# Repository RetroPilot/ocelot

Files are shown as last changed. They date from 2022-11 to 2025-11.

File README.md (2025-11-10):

# Welcome to Ocelot
something, something marketing. do we need to do this? if you don't know, prepare to know.

this is the firmware repository for RetroPilot's family of automotive gateway and control modules.

they allow users to easily retrofit parts from other cars, selectively gateway ECUs at will, filter and convert messages, control actuators, and more.

## Ocleot and Chimera

**[Gateway V2](https://shop.retropilot.org/product/gateway-v2/)** - the CAN gateway of your dreams. gateway messages between buses, retrofit parts, etc.
- gateway and modify CAN messages between multiple buses
- translate signals and convert message formats for part retrofitting
- filter and manipulate specific bits in CAN frames
- enable features by modifying ECU communications
- integrated SSR for connecting and disconnecting busses on-the-fly

**[Chimera](https://shop.retropilot.org/product/chimera/)** - CAN gateway with raw sensor inputs for complete vehicle integration
- has raw sensor inputs for VSS (vehicle speed), CPS (crank position sensor), and ADC (for cruise control stalks)
- can convert existing CAN messages to RetroPilot format for cars that already have some info available over CAN
- has OBD-C connector on-board for connecting to Comma devices
- has USB port on-board and panda-compatible API for sending/recieving messages over CAN
- ideal for vehicles that need CAN gatewaying and/or direct sensor processing in one device

## RetroPilot Cores

**[Actuator Core](https://shop.retropilot.org/product/actuator-core/)** - motor control for steering, throttle, or brake actuators and other automotive applications
- control two DC motors up to 6A each
- build custom actuators for steering, gas, brakes and more

**[Relay Core](https://shop.retropilot.org/product/relay-core/)** - GPIO and relay control with CAN integration
- control lights, fans, pumps, or other 12V devices via CAN messages or GPIO switches
- build custom lighting controllers that respond to vehicle state
- add remote-controlled accessories to your vehicle

**[Interceptor Core](https://shop.retropilot.org/product/interceptor-core/)** - analog sensor interception and injection
- intercept gas pedal signals and modify them for drive-by-wire applications
- modify torque sensor signals for custom steering feel
- add safety limits or filtering to analog sensor inputs

**⚠️ WARNING: Interceptor Core for steering applications is for RESEARCH AND DEVELOPMENT ONLY. Do not use on public roads. Use at your own risk with extreme caution, controlled environments, and always have backup safety systems. RetroPilot assumes no liability for any damages, injuries, or accidents.**

## Hardware
hardware is based on STM32F413 (most modules) or STM32F205 (pedal), and is fully OSHW where applicable. board files, bom, and schematics are located in the `hardware` folder.

## Firmware
firmware borrows heavily from [panda](https://github.com/commaai/panda), and should be firmware-compatible with Panda firmware as a black panda. conversely, most firmware should also work on a panda, which is helpful for development.

### Available Projects:
- `chimera` - Chimera gateway firmware
- `actuator_core` - motor control
- `relay_core` - relay and GPIO control  
- `interceptor_core` - analog sensor interception
- `ibst` - iBooster control
- `smart_dsu` - smart DSU module
- `eps_gw` - EPS gateway
- `steer_actuator_demo` - steering actuator demo
- `panda` - panda compatibility mode
- `pedal` - pedal module (STM32F205)

### Prerequisites:

#### Docker Setup (recommended):
install Docker for your operating system. then build the container:
```
./build_container.sh
```

#### Python Setup (for configuration tool):
install pipenv:
```
pip install pipenv
```
then setup the environment:
```
pipenv install
```

### Flashing:

Docker (recommended):
enter the environment
```
pipenv shell
```
you will want to do this any time you compile firmware, flash, or use the configuration tool. flash the board with
```
./flash_docker.sh <project name>
```

where <project_name> is the board or project you want to flash, for example actuator_core for Actuator Core. providing no arguments will list all projects available to build and flash.

### Configuration tool:

#### Mac/Linux:
enter the pipenv environment:
```
pipenv shell
```
then run the configuration tool:
```
./stm_flash_config.py
```
select the device you'd like to configure and follow the wizard.

##### Configuration by Device:

#### Actuator Core Configuration:

**System Config** - set device operating mode:
- `debug_lvl`: debug output level
- `can_out_en`: enable CAN message transmission
- `iwdg_en`: enable watchdog timer (0 while configuring, 1 when finished)
- `mode`: operating mode (0=Default/USB control, 1=Steer, 2=Cruise)

**TPS Config** - throttle position sensor setup (cruise mode only):
- `adc1`: minimum throttle position (fully closed)
- `adc2`: maximum throttle position (fully open)
- `adc_tolerance`: position control deadzone
- `adc_num`: ADC channel number (0 or 1)

**Motor Config** - throttle motor setup:
- `bridge_channel`: which H-bridge to use (1 or 2)
- `type`: motor function (1=throttle motor)
- `polarity`: motor direction (1=normal, 2=inverted)

**Clutch Config** - clutch motor setup:
- `bridge_channel`: which H-bridge to use (1 or 2)
- `type`: motor function (2=clutch)
- `polarity`: motor direction (1=normal, 2=inverted)

#### Interceptor Core Configuration:

**System Config** - set device operating mode:
- `debug_lvl`: debug output level
- `can_out_en`: enable CAN message transmission
- `iwdg_en`: enable watchdog timer (0 while configuring, 1 when finished)
- `mode`: operating mode (0=Unconfigured, 1=Differential, 2=Gas Pedal)
- `override_threshold`: differential mode threshold (default 336)

**ADC Channel Validation** - sensor validation setup:

*Differential Mode (center point + tolerance):*
- `adc1`: center value (expected sensor position)
- `adc2`: unused (set to 0)
- `adc_tolerance`: deviation tolerance (±)

*Gas Pedal Mode (range limits):*
- `adc1`: maximum valid value (e.g., 4000 for 4.0V)
- `adc2`: minimum valid value (e.g., 200 for 0.2V)
- `adc_tolerance`: hysteresis/noise tolerance

#### Relay Core Configuration:

**System Config** - basic system setup:
- `debug_lvl`: debug output level
- `can_out_en`: enable CAN message transmission
- `iwdg_en`: enable watchdog timer (0 while configuring, 1 when finished)

**Relay Configs** - individual relay setup:
- `label`: predefined automotive function (TURN_L_FRONT, HEAD_L, BRAKE_L, etc.)
- `gpio_en`: enable GPIO control (0 or 1)
- `gpio_bitmask`: GPIO pin combination required
- `can_addr`: CAN message ID to monitor (0 disables)
- `can_cmp_val`: CAN signal value that triggers relay
- `sig_len`/`shift_amt`: CAN signal extraction parameters

#### Chimera Configuration:

**System Config** - basic system setup:
- `debug_lvl`: debug output level
- `can_out_en`: enable CAN message transmission
- `iwdg_en`: enable watchdog timer (0 while configuring, 1 when finished)

**CAN Signal Configs** - gateway message processing:
- `can_id`: which CAN message to process (hex like 0x123)
- `shift_amt`/`sig_len`: which bits contain your signal (shift right X bits, then mask Y bits)
- `scale_mult`/`scale_offs`: math to convert raw values (result = raw * mult + offset)
- `endian_type`: byte order (0=little endian, 1=big endian)
- `is_signed`: treat signal as signed integer or not
- `enabled`: enable this signal processing (0 or 1)

**HALL Sensor Configs** - vehicle speed and engine sensor processing:
- `vss_ppd`: pulses per distance (mile or km)
- `is_km`: use metric units (1=km, 0=miles)
- `rel_cnt`: reluctor tooth count for crank position sensor
- `skipped_teeth`: missing teeth count (e.g., 36-1 = 1 skipped tooth)

**ADC Button Configs** - cruise control button detection:
- `adc1`/`adc2`: threshold values for button states
- `adc_tolerance`: noise tolerance
- `adc_num`: ADC channel for cruise control buttons

#### Any OS:
use the web-based config tool available [here](https://coreconfig.retropilot.org/)

## Documentation
full documentation and examples are available at the [RetroPilot Wiki](https://wiki.retropilot.org/index/hardware/ocelot):

https://wiki.retropilot.org/index/hardware/ocelot

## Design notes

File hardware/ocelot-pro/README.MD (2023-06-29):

# Ocelot Pro Hardware
This directory contains information related to Ocelot Pro hardare. Here, you'll find information about the hardware itself.
## Header Pin Description
### **H1: CAN**
This header contains the three CAN interfaces on the Ocelot Pro, and is organized like so:

| **CAN1** | **CAN2** | **CAN3** |
|---|---|---|
| CAN1L | CAN2L | CAN3L |
| CAN1H | CAN2H | CAN3H |

### **H2: SWD**
This header contains the pins to connect a SWD Link cable. You can use this along with GDB to debug the running application live.

### **H3: POWER**
This header is connected to all power rails in the Ocelot Pro. Each pin is duplicated in case you want to connect multiple peripherals to a rail.

| **PIN** | **Description** |
|---|---|
| IGN_OUT | 12V 3A, switched by pin PA1  |
| 12V | 12V input VIN |
| 5V | 5V 60mA |
| 3.3V | 3.3V 60mA |
| GND | Ground |

### **H4 and H5: GPIO**
All GPIO are 3.3V and connected directly to the STM32F413. Use a level shifter if using 5V logic. Best practice would be to limit the current source/sink to 25mA on a GPIO. More info on this in the datasheet.
Each GPIO can be used as digital I/O or alternate functions depending on the peripheral and the pin. See below:

#### **H4**
| **PIN** | **Alt Functions** |
|---|---|
| **PB10:** | TIM2_CH3, I2C2_SCL, SPI2_SCK/I2S2_CK, I2S3_MCK, USART3_TX, I2CFMP1_SCL, DFSDM2_CKOUT, SDIO_D7, EVENTOUT|
| **PB1:**  | TIM1_CH3N, TIM3_CH4, TIM8_CH3N, SPI5_NSS/I2S5_WS, DFSDM1_DATIN0, QUADSPI_CLK, EVENTOUT |
| **PC5:**  | DFSDM2_DATIN2, I2CFMP1_SMBA, USART3_RX, QUADSPI_BK2_IO3, FSMC_NOE, EVENTOUT |
| **PA7:**  | TIM1_CH1N, TIM3_CH2, TIM8_CH1N, SPI1_MOSI/I2S1_SD, DFSDM2_DATIN1, TIM14_CH1, QUADSPI_BK2_IO1, EVENTOUT |
| **PA5:**  | TIM2_CH1/TIM2_ETR, TIM8_CH1N, SPI1_SCK/I2S1_CK, DFSDM1_CKIN1, FSMC_D7/FSMC_DA7, EVENTOUT |
| **PA3:**  | TIM2_CH4, TIM5_CH4, TIM9_CH2, I2S2_MCK, USART2_RX, SAI1_SD_B, FSMC_D5/FSMC_DA5, EVENTOUT |
| **PC3:**  | LPTIM1_ETR, DFSDM2_CKIN7, SPI2_MOSI/I2S2_SD, SAI1_FS_B, FSMC_A0, EVENTOUT |
| **PC0:**  | LPTIM1_IN1, DFSDM2_CKIN4, SAI1_MCLK_B, EVENTOUT |
| **PC14:** | EVENTOUT |
| **3V3:**  | 3.3V rail |
| **PB2:**  | LPTIM1_OUT, DFSDM1_CKIN0, QUADSPI_CLK, EVENTOUT |
| **PB0:**  | TIM1_CH2N, TIM3_CH3, TIM8_CH2N, SPI5_SCK/I2S5_CK, EVENTOUT |
| **PC4:**  | DFSDM2_CKIN2, I2S1_MCK, QUADSPI_BK2_IO2, FSMC_NE4, EVENTOUT |
| **PA6:**  | TIM1_BKIN, TIM3_CH1, TIM8_BKIN, SPI1_MISO, I2S2_MCK, DFSDM2_CKIN1, TIM13_CH1, QUADSPI_BK2_IO0, SDIO_CMD, EVENTOUT | 
| **PA4:**  | SPI1_NSS/I2S1_WS, SPI3_NSS/I2S3_WS, USART2_CK, DFSDM1_DATIN1, FSMC_D6/FSMC_DA6, EVENTOUT |
| **PA2:**  | TIM2_CH3, TIM5_CH3, TIM9_CH1, I2S2_CKIN, USART2_TX, FSMC_D4/FSMC_DA4, EVENTOUT |
| **PC2:**  | LPTIM1_IN2, DFSDM2_DATIN7, SPI2_MISO, I2S2ext_SD, SAI1_SCK_B, DFSDM1_CKOUT, FSMC_NWE, EVENTOUT |
| **PC15:** | EVENTOUT |
| **NC:** | N/C |
| **GND:**  | Ground |

#### **H5**    
| **PIN** | **Alt Functions** |
|---|---|
| **PB12:** | TIM1_BKIN, I2C2_SMBA, SPI2_NSS/I2S2_WS, SPI4_NSS/I2S4_WS, SPI3_SCK/I2S3_CK, USART3_CK, CAN2_RX, DFSDM1_DATIN1, UART5_RX, FSMC_D13/FSMC_DA13, EVENTOUT | 
| **PB14:** | TIM1_CH2N, TIM8_CH2N, I2CFMP1_SDA, SPI2_MISO, I2S2ext_SD, USART3_RTS, DFSDM1_DATIN2, TIM12_CH1, FSMC_D0/FSMC_DA0, SDIO_D6, EVENTOUT | 
| **PC6:**  | TIM3_CH1, TIM8_CH1, I2CFMP1_SCL, I2S2_MCK, DFSDM1_CKIN3, DFSDM2_DATIN6, USART6_TX, FSMC_D1/FSMC_DA1, SDIO_D6, EVENTOUT |
| **PC8:**  | TIM3_CH3, TIM8_CH3, DFSDM2_CKIN3, USART6_CK, QUADSPI_BK1_IO2, SDIO_D0, EVENTOUT |
| **PA9:**  | TIM1_CH2, DFSDM2_CKIN3, I2C3_SMBA, SPI2_SCK/I2S2_CK, USART1_TX, USB_FS_VBUS, SDIO_D2, EVENTOUT |
| **PC10:** | DFSDM2_CKIN5, SPI3_SCK/I2S3_CK, USART3_TX, QUADSPI_BK1_IO1, SDIO_D2, EVENTOUT |
| **PC12:** | SPI3_MOSI/I2S3_SD, USART3_CK, UART5_TX, FSMC_D3/FSMC_DA3, SDIO_CK, EVENTOUT |
| **PB3:**  | TDO-SWO, TIM2_CH2, I2CFMP1_SDA, SPI1_SCK/I2S1_CK, SPI3_SCK/I2S3_CK, USART1_RX, UART7_RX, I2C2_SDA, SAI1_SD_A, CAN3_RX, EVENTOUT |
| **PB7:**  | LPTIM1_IN2, TIM4_CH2, I2C1_SDA, DFSDM2_DATIN7, USART1_RX, FSMC_NL, EVENTOUT |
| **3V3** | 3.3V rail |
|**PB13:**  | TIM1_CH1N, I2CFMP1_SMBA, SPI2_SCK/I2S2_CK, SPI4_SCK/I2S4_CK, USART3_CTS, CAN2_TX, DFSDM1_CKIN1, UART5_TX, EVENTOUT |
|**PB15:**  | RTC_REFIN, TIM1_CH3N, TIM8_CH3N, I2CFMP1_SCL, SPI2_MOSI/I2S2_SD, DFSDM1_CKIN2, TIM12_CH2, SDIO_CK, EVENTOUT |
|**PC7:** | TIM3_CH2, TIM8_CH2, I2CFMP1_SDA, SPI2_SCK/I2S2_CK, I2S3_MCK, DFSDM2_CKIN6, USART6_RX, DFSDM1_DATIN3, SDIO_D7, EVENTOUT |
|**PC9:** | MCO_2, TIM3_CH4, TIM8_CH4, I2C3_SDA, I2S2_CKIN, DFSDM2_DATIN3, QUADSPI_BK1_IO0, SDIO_D1, EVENTOUT |
|**PA10:**  | TIM1_CH3, DFSDM2_DATIN3, SPI2_MOSI/I2S2_SD, SPI5_MOSI/I2S5_SD, USART1_RX, USB_FS_ID, EVENTOUT |
|**PC11:**  | DFSDM2_DATIN5, I2S3ext_SD, SPI3_MISO, USART3_RX, UART4_RX, QUADSPI_BK2_NCS, FSMC_D2/FSMC_DA2, SDIO_D3, EVENTOUT |
|**PD2:** | TIM3_ETR, DFSDM2_CKOUT, UART5_RX, FSMC_NWE, SDIO_CMD, EVENTOUT |
|**PB4:** | JTRST, TIM3_CH1, SPI1_MISO, SPI3_MISO, I2S3ext_SD, UART7_TX, I2C3_SDA, SAI1_SCK_A, CAN3_TX, SDIO_D0, EVENTOUT |
|**N/C** | N/C |
|**GND** | Ground |

More info on GPIOs can be found in the [datasheet](https://www.st.com/resource/en/datasheet/stm32f423ch.pdf)

## Buttons, Connectors, and Jumpers
Ocelot Pro contains the following buttons:
BOOT (SW1)
RESET (SW2)

The RESET button resets the chip, and if the BOOT button is held while resetting, the device goes into DFU mode.

The USB-C connector is specifically used for CAN traffic analysis / serial debugging / firmware updates. Do not connect a Comma OBD-C cable into this port or you will risk burning up everything on the 5V rail.

## Board Files and Schematic
This directory contains the schematics and Gerber files for Ocelot Pro. Use these to customize the board or build one. Pre-made boards can be purchased at [RetroPilot Shop](https://shop.retropilot.org/product/ocelot-pro-devkit/)

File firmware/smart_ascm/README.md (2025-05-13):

# SmartASCM

## Supported cars
- 2023 Cadillac XT4

## How it Works
the GM brake message gets block by Smart ASCM and replaced with the one sent by the comma

## Installation

install the device with bus 1 connected to the chassis bus at ASCM (with ASCM removed from bus like GM cam harness), bus 2 connected to powertrain expansion at ASCM, and bus 3 connected to chassis of ASCM.

refer to the hardware guide for more info:
https://wiki.retropilot.org/index/hardware/ocelot/hardware

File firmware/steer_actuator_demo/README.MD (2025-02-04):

### Parts

| QTY | PN | Description | 
|-----|---|---|
|1 |BTS7960 | motor driver |
|2 |FIT0493 | 350RPM motor |
|1 |6656K236 | Ultra-Thin Ball Bearing, Steel Ring, Shielded, 60mm Shaft Diameter and 78mm Housing ID  |
|1 |Ocelot Pro | Ocelot Pro CAN Devkit |
|1 |89245-0K020| TOYOTA angle sensor |
|1 | - | 1kOhm Resistor |
|1 | - | toggle switch |

STL Files are in [here](../../hardware/actuator-demo) and were designed by David Abraham (@Vasillo on Discord)

Gear ratio between the motors and final drive gear is 5:1, thus the final torque output is around 9.414384 Nm at peak `((1.176798 Nm /motor * 2 motors) * 0.80 * 5)`

The 1k resistor pulls PB14 up to 3.3v, and the switch pulls the same pin to GND.

### Wiring

|  PIN  |  Function  |
|---|---|
| PB12  | L_ENABLE |
| PB13  | R_ENABLE |
| PB14  | SWITCH IN  |
| PA2 | L_PWM |
| PA3 | R_PWM |

Constant 12V should be used to power the Hbridge VBatt inputs, and a switched 12V should be used to connect the Ocelot Pro's 12V input to power.

#### Angle Sensor
CANL and CANH should be on the same bus as the Ocelot Pro CAN1. Below is a wiring guide.

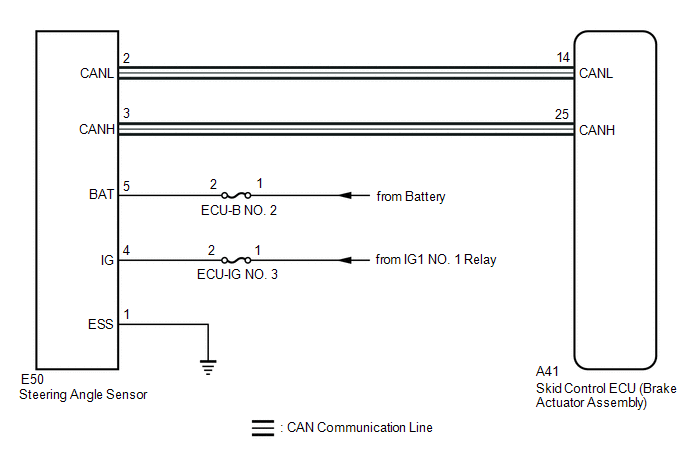
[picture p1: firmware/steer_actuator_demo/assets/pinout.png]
Angle Sensor Pinout


### CAN

This example only uses CAN1 to interface with CAN. Make sure to terminate the bus with a 120 Ohm resistor so everything communicates correctly.

#### Inputs:
0x22E - torque / angle request (angle req is not yet implemented)

#### Outputs:
0x22F - actuator status
0x22D - fake cruise state to engage OP demo

#### DBC Sample

```dbc
BO_ 741 STEERING_COMMAND: 5 EON
 SG_ REQUESTED_STEER_TORQUE : 29|11@1- (0.5,0) [-512|511.5] "Nm" EPAS
 SG_ COUNTER : 8|4@1+ (1,0) [0|15] "" EPAS
 SG_ REQUESTED_STEER_ANGLE : 14|15@1- (0.1,0) [-1638.4|1638.3] "deg" EPAS
 SG_ STEER_MODE : 12|2@1+ (1,0) [0|3] "" EPAS
 SG_ CHECKSUM : 0|8@1+ (1,0) [0|255] "" EPAS

BO_ 608 STEERING_STATUS: 5 EPAS
 SG_ COUNTER : 8|4@1+ (1,0) [0|15] "" EON
 SG_ STATUS : 12|4@1+ (1,0) [0|15] "" EON
 SG_ CHECKSUM : 0|8@1+ (1,0) [0|255] "" EON
 SG_ STEERING_TORQUE_EPS : 29|11@1- (0.8,0) [-819.2|818.4] "Nm" EON
 SG_ STEERING_TORQUE_DRIVER : 18|11@1- (0.8,0) [-819.2|818.4] "Nm" EON
 SG_ STEERING_OK : 16|1@1+ (1,0) [0|1] "" EON

BO_ 37 TOYOTA_STEERING_ANGLE_SENSOR1: 8 TOYOTASAS
 SG_ TOYOTA_STEER_RATE : 35|12@0- (1,0) [-2000|2000] "deg/s" EON
 SG_ TOYOTA_STEER_FRACTION : 39|4@0- (0.1,0) [-0.7|0.7] "deg" EON
 SG_ TOYOTA_STEER_ANGLE : 3|12@0- (1.5,0) [-500|500] "deg" EON

BO_ 870 CURRENT_STATE: 4 EON
 SG_ ENABLED : 8|1@1+ (1,0) [0|0] ""  HIM
 SG_ SET_SPEED : 16|8@1+ (1,0) [0|255] "mph"  HIM
 SG_ CURRENT_SPEED : 24|8@1+ (1,0) [0|255] "kph" IBST
 SG_ CHECKSUM : 0|8@1+ (1,0) [0|255] ""  HIM
```

### Openpilot
**Note: DO NOT UNDER ANY CIRCUMSTANCES INSTALL THIS ON A CAR. DO NOT ATTEMPT TO DRIVE WITH ANY OF THE HARDWARE OR SOFTWARE USED IN THIS DEMO. THIS DEMO IS RELEASED FOR RESEARCH PURPOSES ONLY, AND IS NOT MEANT TO BE USED ON PUBLIC ROADS. ALL INFORMATION AND SOFTWARE IS PROVIDED AS-IS.**

This demo uses an older version of OP that runs on the Eon/C2 or a PC. To connect it in, you will need a Panda (white/grey/black is fine) or a second Ocelot Pro with Panda Shield, relay, and dev harness.

Connect the 12Vbat line to 12V, and ignition to the same switched 12V ignition as the Ocelot. CAN1 and CAN3 from the Panda are bridged together and connected to the CAN bus containing the actuator and the Toyota SAS.

Install the following on an Eon or C2 device:

https://github.com/RetroPilot/openpilot

and checkout branch `actuator_demo`

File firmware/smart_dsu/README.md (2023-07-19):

# SmartDSU

## Supported cars
- 2017-2019 Toyota Corolla
- 2016-2018 Toyota Rav4 (and Hybrid)
- 2016-2019 Toyota Prius
- other DSU-equipped Toyotas with 0x343 as the ACC message

## Supported cars with slight firmware changes
- 2018 Camry Hybrid (tested by @halfcocked)
- 2022 RAV4 Hybrid (tested by @sky)

## How it Works
the Toyota ACC message 0x343 is read in on bus 3 of the gateway, modified, re-checksummed, then sent on to bus 1. if the ACC control message 0x343 is detected on bus 1, it will be blocked from bus 3 entirely. if the alt ACC control message 0xF10 is detected, the smartDSU will modify the forwarded 0x343 with data from inside 0xF10. this method ensures perfect message send rate preservation between the DSU and the vehicle CAN bus. 

a similar approach is taken with AEB message 0x344. if 0xF11 is detected on bus 1, the device will modify the Toyota AEB message, allowing for non-acc brake control without disturbing the stock AEB system.

all other messages are forwarded as-is between the DSU and the car.

if the device detects that 0xF10, 0xF11, or 0x343 is not sent, it will timeout functionality accordingly and restore forwarding between the DSU and the vehicle.

## Installation

install the device with bus 1 facing the CAR CAN and bus 3 facing the DSU or radar. ensure bus 3 is terminated by applying a blob of solder to JL2 (on ocelot pro) or the solder bridge next to CAN3 (on ocelot gateway.)

refer to the hardware guide for more info:
https://wiki.retropilot.org/index/hardware/ocelot/hardware

## Modifying for cars that do not require PERMIT_BRAKING and others
in main.c the following lines of code must be modified to prevent modification of the ACC message since it will be handled by Openpilot instead:

```c
          if(dat[7] == toyota_checksum(address, dat, 8)) {
            // add permit_braking and recompute the checksum
            dat[2] &= 0x3F; // mask off the top 2 bits
            dat[2] |= (1 << 6U); // SET_ME_X01
            dat[3] |= (1 << 6U); // permit_braking
            dat[7] = toyota_checksum(address, dat, 8); 
```

simply comment out the mask and the bitwise math:

```c
          if(dat[7] == toyota_checksum(address, dat, 8)) {
            // add permit_braking and recompute the checksum
            //dat[2] &= 0x3F; // mask off the top 2 bits
            //dat[2] |= (1 << 6U); // SET_ME_X01
            //dat[3] |= (1 << 6U); // permit_braking
            //dat[7] = toyota_checksum(address, dat, 8); 
```

and flash the firmware

```bash
cd ocelot/firmware/smart_dsu
# now put the device into recovery mode by holding BOOT and pressing RESET
./recover.sh
```

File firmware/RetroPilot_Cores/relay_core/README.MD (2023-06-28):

# Ocelot Pro GPIO example
## Introduction
This code functions as sort of an introduction to Ocelot / Panda / STM32 bare metal programming. The purpose is to show users how to set up interfaces on this platform using the Comma AI Panda codebase as a skeleton to build things on top. Maybe you want to build a CAN controlled relay and install it in a car. How would you go about doing that? Well a good place to start would be [Comma's Panda code](https://github.com/commaai/panda), since it aims to be compliant with MISRA and potentially ASIL. After that, it's a matter of grabbing an [Ocelot Pro](https://shop.retropilot.org/product/ocelot-pro-devkit/), setting up GPIOs, then connecting all that to the CAN interface so the GPIO responds to your custom CAN message.

That is where this example will hopefully help you out.

## What is covered here
We will do the following here:
- CAN interfaces setup (CAN1, CAN2, CAN3)
- Timer setup
- PWM setup
- GPIO setup

You will want a decent working knowledge of how to read code, preferably C. I'm not sure this would classify as a "beginner guide" per se, but if you're familiar with Arduino to some extent this should be somewhat approachable. We will not go too far in depth in terms of how the registers are actually set, nor what memory addresses and individual bits are actually set. So I guess difficulty: intermediate? Nothing to be scared of!

## Pins

PA2 - PWM (TIM5_CH3)
PA3 - PWM (TIM5_CH4)
PB12 - GPIO (digital out)
PB13 - GPIO (digital out)

Connect up to a scope, LEDs, h-bridge, whatever. Make sure to connect via a resistor (like 220 ohm or something) if using LEDs.

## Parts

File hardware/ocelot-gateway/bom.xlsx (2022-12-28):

No. | Quantity | Comment | Designator | Footprint | Value | Manufacturer Part | Manufacturer | Supplier Part | Supplier
1 | 2 | 22p | C1,C2 | 0603-C
2 | 2 | 4.7u | C3,C4 | 0603-C
3 | 10 | 100n | C5,C6,C7,C8,C9,C10,C11,C12,C13,C14 | 0603-C
4 | 2 | 2.2u | C15,C16 | 0603-C
5 | 1 | BAS40 | D1 | SOT23
6 | 1 | MIC5233-3.3YM5-TR | IC1 | SOT95P280X145-5N
7 | 1 |  | J1 | USB-C-BREAKOUT_SPARKFUN-CONNECTORS_USB-C-16P
8 | 3 |  | J2,J3,J4 | 1X02
9 | 1 |  | J5 | 1X04
10 | 1 |  | J6 | 1X05_1.27MM
11 | 1 | MIC5233-5.0YM5-TR | PS1 | SOT95P280X145-5N
12 | 1 | PMOSFET | Q1 | SOT23
13 | 1 | NMOSFET | Q2 | SOT23
14 | 2 | 22 | R1,R2 | 0402-R
15 | 2 | 5.1k | R3,R4 | 0402-R
16 | 2 | 120 | R5,R6 | 0402-R
17 | 4 | 10k | R7,R8,R9,R10 | 0402-R
18 | 2 | MOMENTARY-SWITCH-SPST-SMD-6.0X3.5MM | S1,S2 | TACTILE_SWITCH_SMD_6.0X3.5MM
19 | 2 |  | SJ1,SJ2 | SJ
20 | 1 | STM32F413RGT6 | U1 | LQFP64-10X10MM
21 | 3 | TJA1042 | U2,U3,U4 | NXP_SEMICONDUCTORS_TJA1042T-3-CM_118_0
22 | 1 | CRYSTAL-3.2X2.54-PIN | Y1 | XTAL-3.2X2.5

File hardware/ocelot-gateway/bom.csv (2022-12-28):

Part | Value | Device | Package | Description
C1 | 22p | C0603 | 0603-C
C2 | 22p | C0603 | 0603-C
C3 | 4.7u | C0603 | 0603-C
C4 | 4.7u | C0603 | 0603-C
C5 | 100n | C0603 | 0603-C
C6 | 100n | C0603 | 0603-C
C7 | 100n | C0603 | 0603-C
C8 | 100n | C0603 | 0603-C
C9 | 100n | C0603 | 0603-C
C10 | 100n | C0603 | 0603-C
C11 | 100n | C0603 | 0603-C
C12 | 100n | C0603 | 0603-C
C13 | 100n | C0603 | 0603-C
C14 | 100n | C0603 | 0603-C
C15 | 2.2u | C0603 | 0603-C
C16 | 2.2u | C0603 | 0603-C
D1 | BAS40 | BAS40 | SOT23 | Silicon Schottky Diodes
IC1 | MIC5233-3.3YM5-TR | MIC5233-3.3YM5-TR | SOT95P280X145-5N | High Input Voltage Low IQ UCAP LDO Regulator
J1 |  | USB-C-BREAKOUT_SPARKFUN-CONNECTORS_USB_C16PIN | USB-C-BREAKOUT_SPARKFUN-CONNECTORS_USB-C-16P | USB Type C 16Pin Connector
J2 |  | CONN_02 | 1X02 | Multi connection point. Often used as Generic Header-pin footprint for 0.1 inch
J3 |  | CONN_02 | 1X02 | Multi connection point. Often used as Generic Header-pin footprint for 0.1 inch
J4 |  | CONN_02 | 1X02 | Multi connection point. Often used as Generic Header-pin footprint for 0.1 inch
J5 |  | CONN_04 | 1X04 | Multi connection point. Often used as Generic Header-pin footprint for 0.1 inch
PS1 | MIC5233-5.0YM5-TR | MIC5233-5.0YM5-TR | SOT95P280X145-5N | MICROCHIP - MIC5233-5.0YM5-TR - LDO, REG, 36VIN, 0.1A, 5V, 2%, 5SOT23
Q1 | PMOSFET | PMOSFET_SOT23 | SOT23 | P-Channel MOSFET - Generic
Q2 | NMOSFET | NMOSFETSOT23 | SOT23 | N-Channel MOSFET - Generic
R1 | 22 | R0402 | 0402-R
R2 | 22 | R0402 | 0402-R
R3 | 5.1k | R0402 | 0402-R
R4 | 5.1k | R0402 | 0402-R
R5 | 120 | R0402 | 0402-R
R6 | 120 | R0402 | 0402-R
R7 | 10k | R0402 | 0402-R
R8 | 10k | R0402 | 0402-R
R9 | 10k | R0402 | 0402-R
R10 | 10k | R0402 | 0402-R
S1 | MOMENTARY-SWITCH-SPST-SMD-6.0X3.5MM | MOMENTARY-SWITCH-SPST-SMD-6.0X3.5MM | TACTILE_SWITCH_SMD_6.0X3.5MM | Momentary Switch (Pushbutton) - SPST
S2 | MOMENTARY-SWITCH-SPST-SMD-6.0X3.5MM | MOMENTARY-SWITCH-SPST-SMD-6.0X3.5MM | TACTILE_SWITCH_SMD_6.0X3.5MM | Momentary Switch (Pushbutton) - SPST
SJ1 |  | SJ | SJ | SMD solder JUMPER
SJ2 |  | SJ | SJ | SMD solder JUMPER
U1 | STM32F413RGT6 | STM32F413RGT6 | LQFP64-10X10MM
U2 | TJA1042 | TJA1042 | NXP_SEMICONDUCTORS_TJA1042T-3-CM_118_0
U3 | TJA1042 | TJA1042 | NXP_SEMICONDUCTORS_TJA1042T-3-CM_118_0
U4 | TJA1042 | TJA1042 | NXP_SEMICONDUCTORS_TJA1042T-3-CM_118_0
Y1 | CRYSTAL-3.2X2.54-PIN | CRYSTAL-3.2X2.54-PIN | XTAL-3.2X2.5

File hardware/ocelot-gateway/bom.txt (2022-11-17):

Part Value                               Device                                        Package                                      Description                                                                                                     BUILT_BY    CATEGORY   COPYRIGHT                                                   DESCRIPTION                                                           DRAIN_CURRENT HEIGHT MANUFACTURER MANUFACTURER_NAME MANUFACTURER_PART_NUMBER MOUSER_PART_NUMBER   MOUSER_PRICE-STOCK                                                                                                  MPN OPERATING_TEMP PART_STATUS POPULARITY PROD_ID    ROHS_COMPLIANT SERIES SF_SKU    SOURCELIBRARY                  SUB-CATEGORY THERMALLOSS TYPE      VALUE   VENDOR            
C1   22p                                 C0603                                         0603-C                                                                                                                                                                                                                                                                                                                                                                                                                                                                                                                                                                                                                                                                                                                       
C2   22p                                 C0603                                         0603-C                                                                                                                                                                                                                                                                                                                                                                                                                                                                                                                                                                                                                                                                                                                       
C3   4.7u                                C0603                                         0603-C                                                                                                                                                                                                                                                                                                                                                                                                                                                                                                                                                                                                                                                                                                                       
C4   4.7u                                C0603                                         0603-C                                                                                                                                                                                                                                                                                                                                                                                                                                                                                                                                                                                                                                                                                                                       
C5   100n                                C0603                                         0603-C                                                                                                                                                                                                                                                                                                                                                                                                                                                                                                                                                                                                                                                                                                                       
C6   100n                                C0603                                         0603-C                                                                                                                                                                                                                                                                                                                                                                                                                                                                                                                                                                                                                                                                                                                       
C7   100n                                C0603                                         0603-C                                                                                                                                                                                                                                                                                                                                                                                                                                                                                                                                                                                                                                                                                                                       
C8   100n                                C0603                                         0603-C                                                                                                                                                                                                                                                                                                                                                                                                                                                                                                                                                                                                                                                                                                                       
C9   100n                                C0603                                         0603-C                                                                                                                                                                                                                                                                                                                                                                                                                                                                                                                                                                                                                                                                                                                       
C10  100n                                C0603                                         0603-C                                                                                                                                                                                                                                                                                                                                                                                                                                                                                                                                                                                                                                                                                                                       
C11  100n                                C0603                                         0603-C                                                                                                                                                                                                                                                                                                                                                                                                                                                                                                                                                                                                                                                                                                                       
C12  100n                                C0603                                         0603-C                                                                                                                                                                                                                                                                                                                                                                                                                                                                                                                                                                                                                                                                                                                       
C13  100n                                C0603                                         0603-C                                                                                                                                                                                                                                                                                                                                                                                                                                                                                                                                                                                                                                                                                                                       
C14  100n                                C0603                                         0603-C                                                                                                                                                                                                                                                                                                                                                                                                                                                                                                                                                                                                                                                                                                                       
C15  2.2u                                C0603                                         0603-C                                                                                                                                                                                                                                                                                                                                                                                                                                                                                                                                                                                                                                                                                                                       
C16  2.2u                                C0603                                         0603-C                                                                                                                                                                                                                                                                                                                                                                                                                                                                                                                                                                                                                                                                                                                       
D1   BAS40                               BAS40                                         SOT23                                        Silicon Schottky Diodes                                                                                                                                                                                                                                                                                                                                                                                                                                                                                                       0                                                                                                                                                 
IC1  MIC5233-3.3YM5-TR                   MIC5233-3.3YM5-TR                             SOT95P280X145-5N                             High Input Voltage Low IQ UCAP LDO Regulator                                                                                                                                                       High Input Voltage Low IQ UCAP LDO Regulator                                        1.45mm              Microchip         MIC5233-3.3YM5-TR        998-MIC5233-3.3YM5TR https://www.mouser.co.uk/ProductDetail/Microchip-Technology-Micrel/MIC5233-33YM5-TR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                                                                                                                                                                                  
J1                                       USB-C-BREAKOUT_SPARKFUN-CONNECTORS_USB_C16PIN USB-C-BREAKOUT_SPARKFUN-CONNECTORS_USB-C-16P USB Type C 16Pin Connector                                                                                                                                                                                                                                                                                                                                                                                                                                                                                                               CONN-14122                                                                                                                             
J2                                       CONN_02                                       1X02                                         Multi connection point. Often used as Generic Header-pin footprint for 0.1 inch spaced/style header connections                                                                                                                                                                                                                                                                                                                                                                                                                                                                                                                                                                 
J3                                       CONN_02                                       1X02                                         Multi connection point. Often used as Generic Header-pin footprint for 0.1 inch spaced/style header connections                                                                                                                                                                                                                                                                                                                                                                                                                                                                                                                                                                 
J4                                       CONN_02                                       1X02                                         Multi connection point. Often used as Generic Header-pin footprint for 0.1 inch spaced/style header connections                                                                                                                                                                                                                                                                                                                                                                                                                                                                                                                                                                 
J5                                       CONN_04                                       1X04                                         Multi connection point. Often used as Generic Header-pin footprint for 0.1 inch spaced/style header connections                                                                                                                                                                                                                                                                                                                                                                                                                          CONN-09696                                                                                                                             
PS1  MIC5233-5.0YM5-TR                   MIC5233-5.0YM5-TR                             SOT95P280X145-5N                             MICROCHIP - MIC5233-5.0YM5-TR - LDO, REG, 36VIN, 0.1A, 5V, 2%, 5SOT23                                                                                                                              MICROCHIP - MIC5233-5.0YM5-TR - LDO, REG, 36VIN, 0.1A, 5V, 2%, 5SOT23               1.45mm              Microchip         MIC5233-5.0YM5-TR        998-MIC5233-5.0YM5TR https://www.mouser.co.uk/ProductDetail/Microchip-Technology-Micrel/MIC5233-50YM5-TR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                                                                                                                                                                                  
Q1   PMOSFET                             PMOSFET_SOT23                                 SOT23                                        P-Channel MOSFET - Generic                                                                                                  Transistor                                                                                                                                                                                                                                                                                                                                                                                                                                                                             MOSFET                   P-Channel PMOSFET                   
Q2   NMOSFET                             NMOSFETSOT23                                  SOT23                                        N-Channel MOSFET - Generic                                                                                                  Transistor                                                                                                                                                                                                                                                                                                                                                                                                                                                                             MOSFET                   N-Channel NMOSFET                   
R1   22                                  R0402                                         0402-R                                                                                                                                                                                                                                                                                                                                                                                                                                                                                                                                                                                                                                                                                                                       
R2   22                                  R0402                                         0402-R                                                                                                                                                                                                                                                                                                                                                                                                                                                                                                                                                                                                                                                                                                                       
R3   5.1k                                R0402                                         0402-R                                                                                                                                                                                                                                                                                                                                                                                                                                                                                                                                                                                                                                                                                                                       
R4   5.1k                                R0402                                         0402-R                                                                                                                                                                                                                                                                                                                                                                                                                                                                                                                                                                                                                                                                                                                       
R5   120                                 R0402                                         0402-R                                                                                                                                                                                                                                                                                                                                                                                                                                                                                                                                                                                                                                                                                                                       
R6   120                                 R0402                                         0402-R                                                                                                                                                                                                                                                                                                                                                                                                                                                                                                                                                                                                                                                                                                                       
R7   10k                                 R0402                                         0402-R                                                                                                                                                                                                                                                                                                                                                                                                                                                                                                                                                                                                                                                                                                                       
R8   10k                                 R0402                                         0402-R                                                                                                                                                                                                                                                                                                                                                                                                                                                                                                                                                                                                                                                                                                                       
R9   10k                                 R0402                                         0402-R                                                                                                                                                                                                                                                                                                                                                                                                                                                                                                                                                                                                                                                                                                                       
R10  10k                                 R0402                                         0402-R                                                                                                                                                                                                                                                                                                                                                                                                                                                                                                                                                                                                                                                                                                                       
S1   MOMENTARY-SWITCH-SPST-SMD-6.0X3.5MM MOMENTARY-SWITCH-SPST-SMD-6.0X3.5MM           TACTILE_SWITCH_SMD_6.0X3.5MM                 Momentary Switch (Pushbutton) - SPST                                                                                                                                                                                                                                                                                                                                                                                                                                                                                                     SWCH-00815                       COM-08229
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

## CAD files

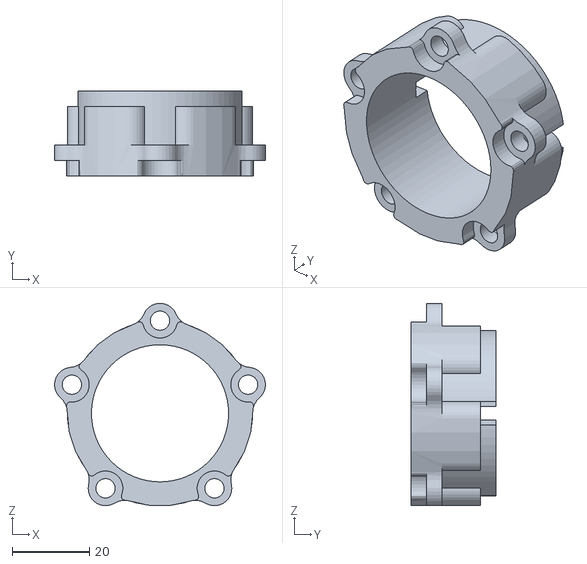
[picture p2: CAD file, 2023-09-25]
hardware/actuator-demo/sas_ring.stl
54.6 x 22.0 x 52.4

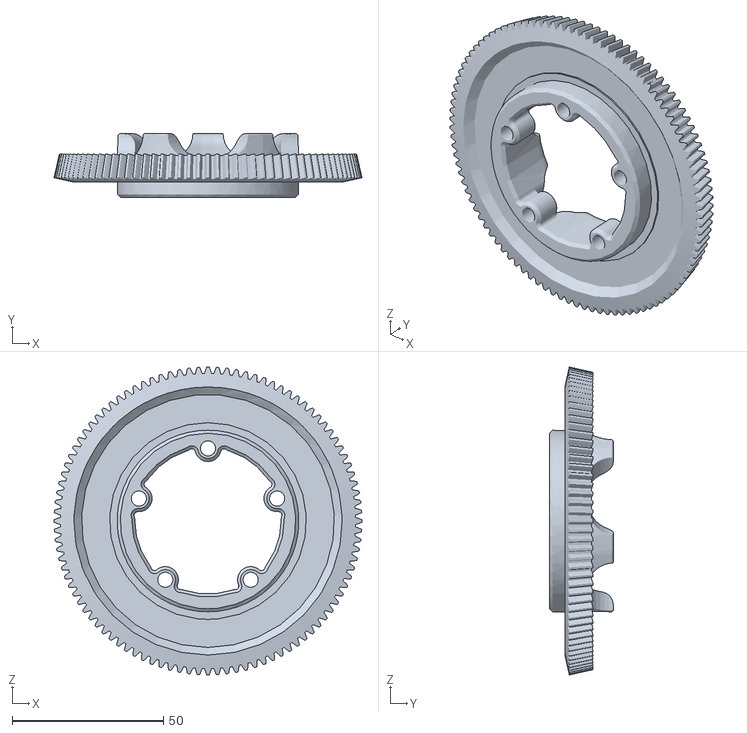
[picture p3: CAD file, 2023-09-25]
hardware/actuator-demo/driven_gear.stl
101.8 x 21.0 x 101.8

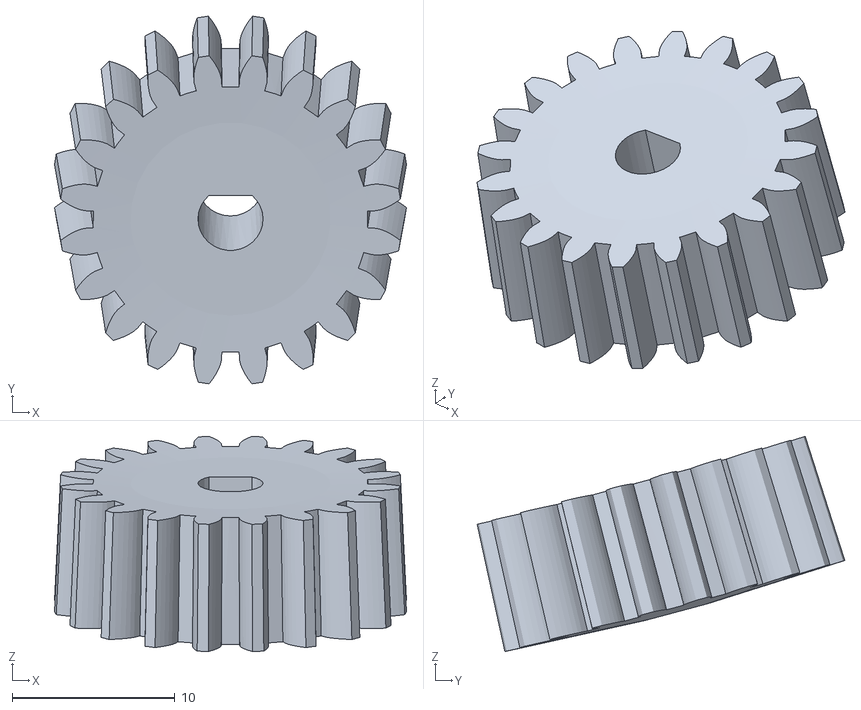
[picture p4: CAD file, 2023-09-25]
hardware/actuator-demo/motor_gear.stl
21.6 x 22.6 x 13.2

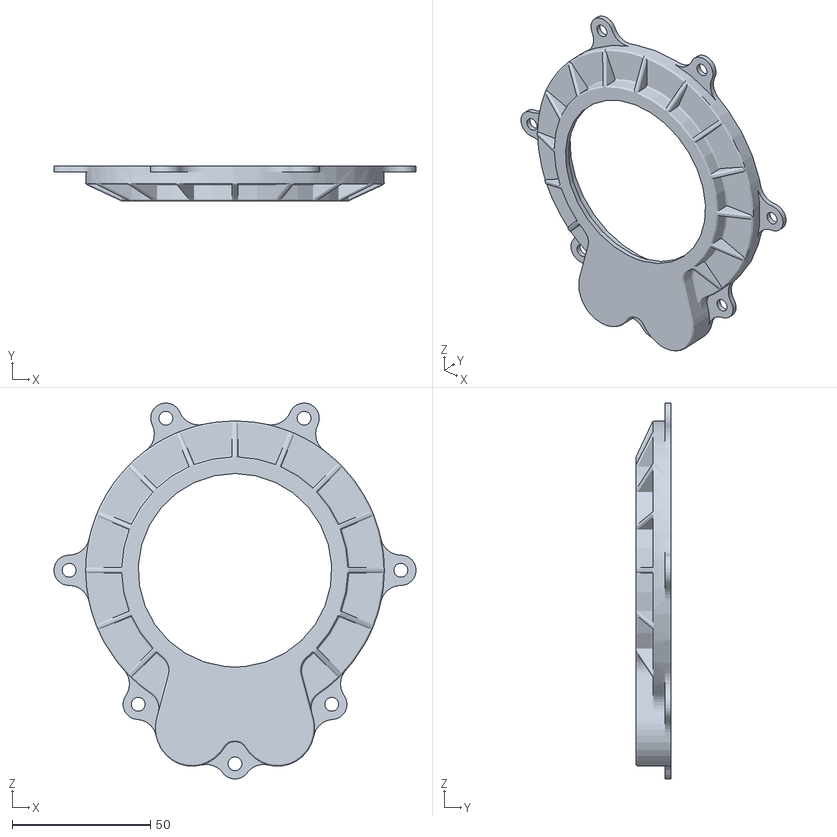
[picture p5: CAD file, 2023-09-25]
hardware/actuator-demo/casing_front.stl
130.9 x 12.5 x 135.9

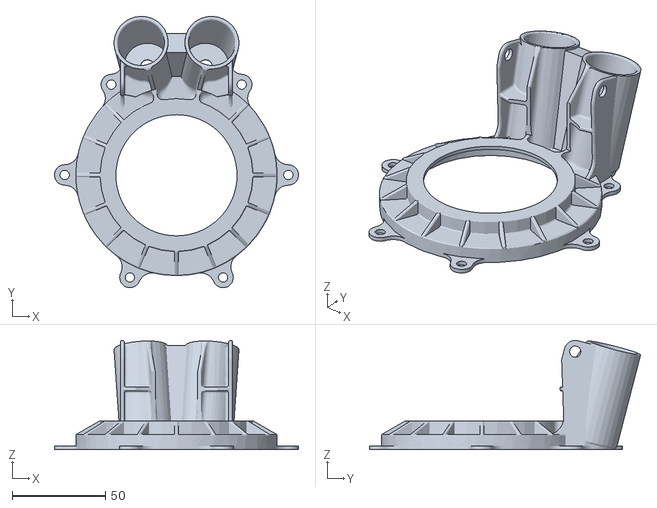
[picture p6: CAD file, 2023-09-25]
hardware/actuator-demo/casing_rear.stl
130.9 x 145.6 x 58.6

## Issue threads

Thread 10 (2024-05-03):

Unable to view schematic

danielkucera, 2024-05-03:
Hello,
I am trying to view the schematic of ocelot pro but no online viewer, not kicad is able to view it. All showing errors.
Can you please ensure all dependencies are included?
Or include PDF export?

danielkucera, 2024-05-03:
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

danielkucera, 2024-06-27:
I managed to open it in latest KiCAD
[ocelot-pro-schematic.pdf](https://github.com/user-attachments/files/16009342/ocelot-pro-schematic.pdf)

Closed 2024-06-27.

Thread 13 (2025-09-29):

Interceptor Core: create pedal control mode

wocsor, 2025-09-29:
Interceptor Core should be able to operate as a pedal. Criteria for this issue:
- implement Pedal CAN I/O message address and structures
- implement pedal control loop (ADC/DAC setting)
- handle relay based on device states

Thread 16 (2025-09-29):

Chimera: Engine CPS tooth count with skipped tooth, flash settings

wocsor, 2025-09-29:
Chimera has an input for CPS pulse, and the interrupt for it is already set up. This feature, when implemented, can be useful for applications such as digital dashboards, remote starters, and upshift indicators. What needs to be done:
- setup new flash struct for engine RPM sensor (or maybe add it to VSS?)
- write config
- implement CPS tooth count and skipped tooth handling in cps_pulse to eng_rpm function
Output of the engine RPM message is already handled and DBC is defined.

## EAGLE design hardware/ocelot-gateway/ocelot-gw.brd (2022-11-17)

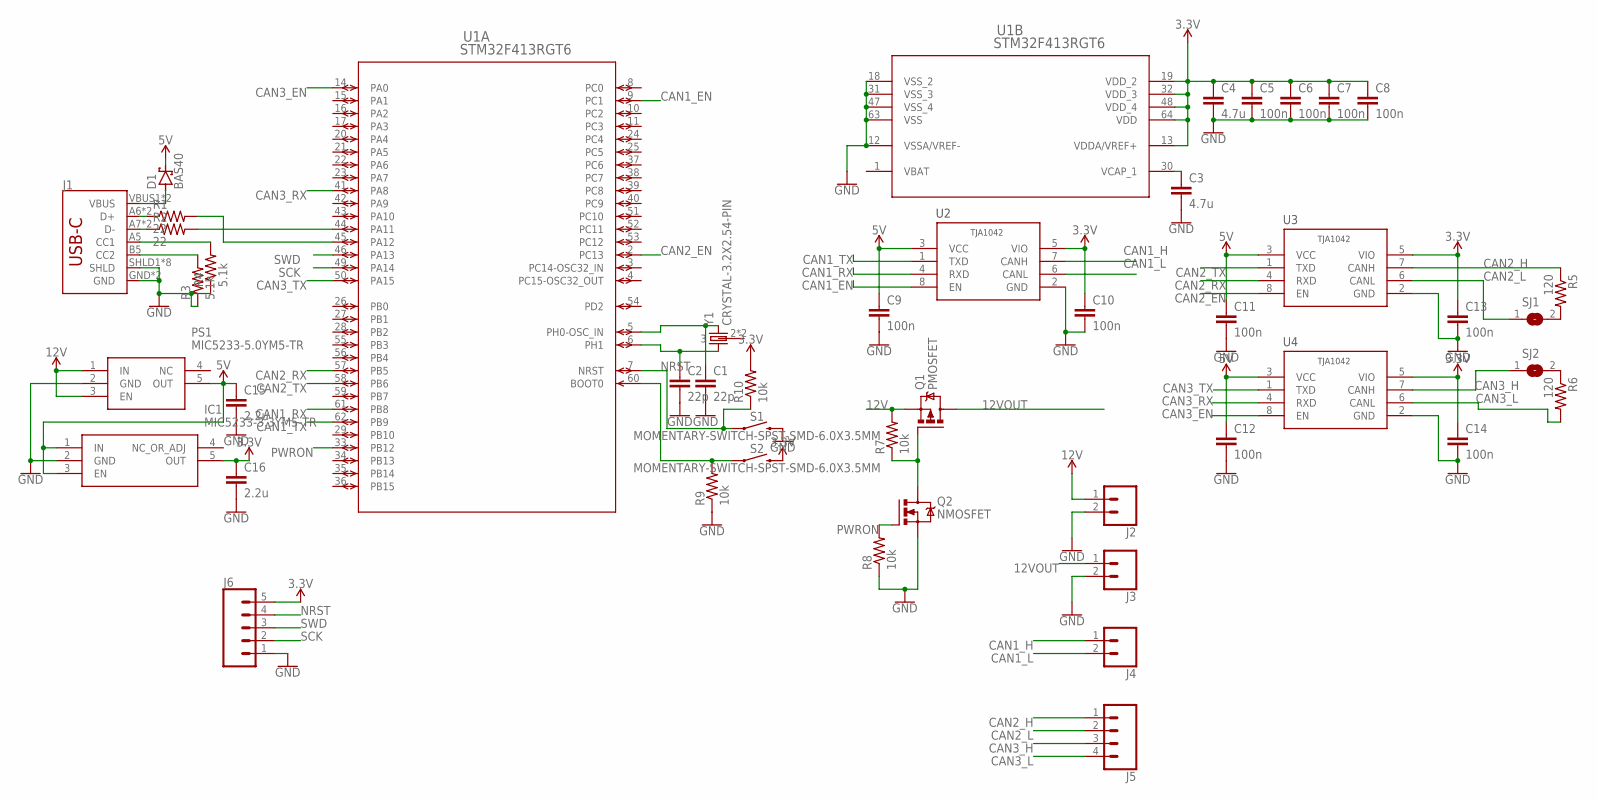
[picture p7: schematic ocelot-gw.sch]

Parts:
C1, C2: 22p; 0603-C
C3, C4: 4.7u; 0603-C
C5, C6, C7, C8, C9, C10, C11, C12, C13, C14: 100n; 0603-C
C15, C16: 2.2u; 0603-C
D1: BAS40; SOT23
IC1: MIC5233-3.3YM5-TR; SOT95P280X145-5N
J1: USB-C-BREAKOUT_SPARKFUN-CONNECTORS_USB_C16PIN; USB-C-BREAKOUT_SPARKFUN-CONNECTORS_USB-C-16P
J2, J3, J4: CONN_02; 1X02
J5: CONN_04; 1X04
J6: CONN_051.27MM; 1X05_1.27MM
PS1: MIC5233-5.0YM5-TR; SOT95P280X145-5N
Q1: PMOSFET; SOT23
Q2: NMOSFET; SOT23
R1, R2: 22; 0402-R
R3, R4: 5.1k; 0402-R
R5, R6: 120; 0402-R
R7, R8, R9, R10: 10k; 0402-R
S1, S2: MOMENTARY-SWITCH-SPST-SMD-6.0X3.5MM; TACTILE_SWITCH_SMD_6.0X3.5MM
SJ1, SJ2: SJ
U1: STM32F413RGT6; LQFP64-10X10MM
U2, U3, U4: TJA1042; NXP_SEMICONDUCTORS_TJA1042T-3-CM_118_0
Y1: CRYSTAL-3.2X2.54-PIN; XTAL-3.2X2.5

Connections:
3.3V: C4.1, C5.1, C6.1, C7.1, C8.1, C10.1, C13.1, C14.1, C16.1, IC1.5 (OUT), J6.5, R10.2, S2.2, U1.13 (VDDA/VREF+), U1.19 (VDD_2), U1.32 (VDD_3), U1.48 (VDD_4), U1.64 (VDD), U2.5 (VIO), U3.5 (VIO), U4.5 (VIO)
5V: C9.1, C11.1, C12.1, C15.1, D1.3 (C), IC1.1 (IN), IC1.3 (EN), PS1.5 (OUT), U2.3 (VCC), U3.3 (VCC), U4.3 (VCC)
12V: J2.1, PS1.1 (IN), PS1.3 (EN), Q1.2 (S), R7.2
12VOUT: J3.1, Q1.3 (D)
CAN1_EN: U1.9 (PC1), U2.8 (EN)
CAN1_H: J4.1, U2.7 (CANH)
CAN1_L: J4.2, U2.6 (CANL)
CAN1_RX: U1.61 (PB8), U2.4 (RXD)
CAN1_TX: U1.62 (PB9), U2.1 (TXD)
CAN2_EN: U1.2 (PC13), U3.8 (EN)
CAN2_H: J5.1, R5.1, U3.7 (CANH)
CAN2_L: J5.2, SJ1.1, U3.6 (CANL)
CAN2_RX: U1.57 (PB5), U3.4 (RXD)
CAN2_TX: U1.58 (PB6), U3.1 (TXD)
CAN3_EN: U1.14 (PA0), U4.8 (EN)
CAN3_H: J5.3, SJ2.1, U4.7 (CANH)
CAN3_L: J5.4, R6.2, U4.6 (CANL)
CAN3_RX: U1.41 (PA8), U4.4 (RXD)
CAN3_TX: U1.50 (PA15), U4.1 (TXD)
GND: C1.2, C2.2, C3.2, C4.2, C5.2, C6.2, C7.2, C8.2, C9.2, C10.2, C11.2, C12.2, C13.2, C14.2, C15.2, C16.2, IC1.2 (GND), J1.GND, J1.GND2 (GND), J1.SHLD1 (SHLD), J1.SHLD2 (SHLD), J1.SHLD3 (SHLD), J1.SHLD4 (SHLD), J1.SHLD5 (SHLD), J1.SHLD6 (SHLD), J1.SHLD7 (SHLD), J1.SHLD8 (SHLD), J2.2, J3.2, J6.1, PS1.2 (GND), Q2.2 (S), R3.1, R4.1, R8.1, R9.1, S1.2, U1.12 (VSSA/VREF-), U1.18 (VSS_2), U1.31 (VSS_3), U1.47 (VSS_4), U1.63 (VSS), U2.2 (GND), U3.2 (GND), U4.2 (GND)
unnamed: C1.1, U1.5 (PH0-OSC_IN), Y1.3 (2)
unnamed: C2.1, U1.6 (PH1), Y1.1
unnamed: R2.2, U1.44 (PA11)
unnamed: R1.2, U1.45 (PA12)
unnamed: D1.1 (A), J1.VBUS1 (VBUS), J1.VBUS2 (VBUS)
unnamed: J1.A5 (CC1), R4.2
unnamed: J1.B5 (CC2), R3.2
unnamed: R9.2, S2.1, U1.60 (BOOT0)
unnamed: J1.A6 (D+), J1.B6 (D+), R1.1
unnamed: J1.A7 (D-), J1.B7 (D-), R2.1
unnamed: R5.2, SJ1.2
unnamed: C3.1, U1.30 (VCAP_1)
unnamed: R6.1, SJ2.2
unnamed: Q1.1 (G), Q2.3 (D), R7.1
NRST: J6.4, R10.1, S1.1, U1.7 (NRST)
PWRON: Q2.1 (G), R8.2, U1.33 (PB12)
SCK: J6.2, U1.49 (PA14)
SWD: J6.3, U1.46 (PA13)
VBAT: U1.1 (VBAT)

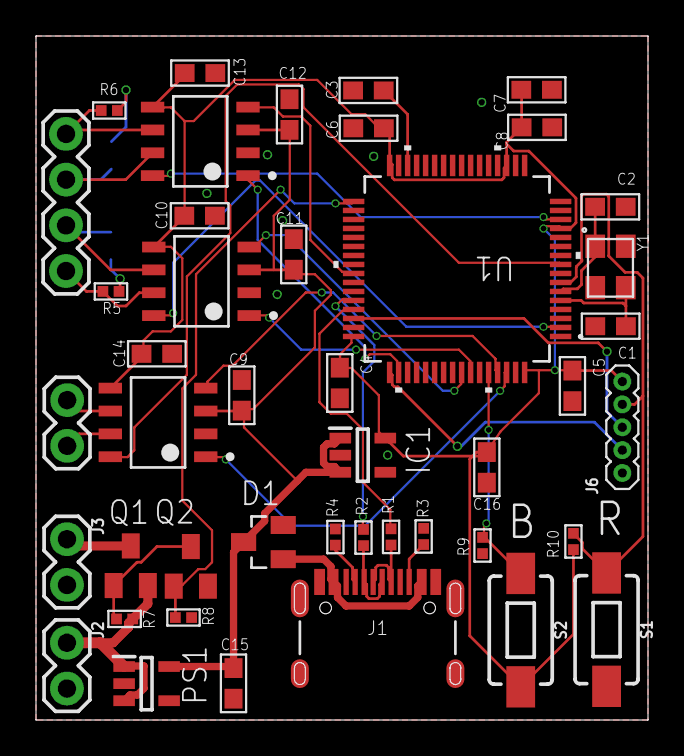
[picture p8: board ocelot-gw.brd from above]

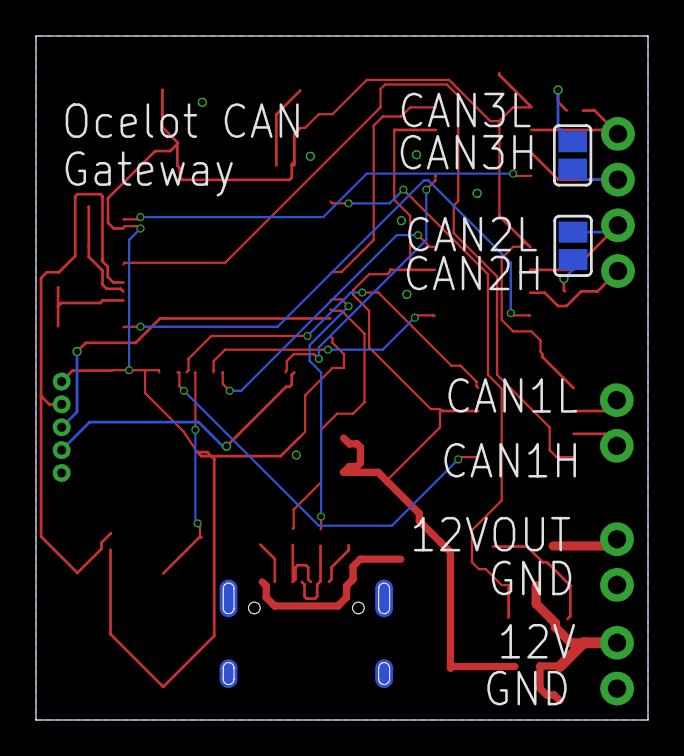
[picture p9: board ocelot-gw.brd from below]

Board: 2 copper layers, 34.0 x 38.0 mm, 46 parts (2 on the bottom side), 38 nets.

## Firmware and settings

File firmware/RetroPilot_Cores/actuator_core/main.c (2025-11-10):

// Includes
#include "../../config.h"
#include "libc.h"

#include "main_declarations.h"
#include "critical.h"
#include "faults.h"

#include "drivers/registers.h"
#include "drivers/interrupts.h"
#include "drivers/llcan.h"
#include "drivers/llgpio.h"
#include "drivers/adc.h"

#include "board.h"

#include "drivers/clock.h"
#include "drivers/timer.h"

#include "gpio.h"
#include "crc.h"

#include "drivers/pwm.h"
// #include "drivers/uart.h"
#include "drivers/json_rpc.h"

#define USB_STRING_DESCRIPTORS

#define STRING_DESCRIPTOR_HEADER(size) \
  (((((size) * 2) + 2) & 0xFF) | 0x0300)

static const uint16_t string_manufacturer_desc[] = {
  STRING_DESCRIPTOR_HEADER(10),
  'R','e','t','r','o','P','i','l','o','t'
};

static const uint16_t string_product_desc[] = {
  STRING_DESCRIPTOR_HEADER(13),
  'A','c','t','u','a','t','o','r',' ','C','o','r','e'
};

// Null functions to replace UART functionality
void puts(const char *a) { UNUSED(a); }
void putch(const char a) { UNUSED(a); }
void puth(unsigned int i) { UNUSED(i); }
void puth2(unsigned int i) { UNUSED(i); }

#include "chimera/usb.h"
#include "chimera/chimera.h"

// USB data buffer (defined in usb.h but need to declare extern)
extern uint8_t usbdata[0x100];

#define DEBUG

uint32_t enter_bootloader_mode;

uint32_t ctrl_timeout = 0;
volatile bool usb_ctrl_active = false;

// cppcheck-suppress unusedFunction ; used in headers not included in cppcheck
void __initialize_hardware_early(void) {
  early();
}
#include "RetroPilot_Cores/actuator_core/can.h"

// Mode definitions
#define MODE_DEFAULT 0
#define MODE_STEER   1
#define MODE_CRUISE  2

// Mode headers
#include "RetroPilot_Cores/actuator_core/modes/common.h"
#include "RetroPilot_Cores/actuator_core/modes/default.h"
#include "RetroPilot_Cores/actuator_core/modes/steer.h"
#include "RetroPilot_Cores/actuator_core/modes/cruise.h"
#include "RetroPilot_Cores/actuator_core/json_rpc_handlers.h"

// Mode function pointers
void (*mode_init_func)(void);
void (*mode_process_func)(void);
void (*mode_can_rx_handler_func)(int address, uint8_t *dat);
void (*mode_timer_handler_func)(void);

uint8_t current_mode = MODE_DEFAULT;

uint8_t motor1_pwm = 0;
uint8_t motor2_pwm = 0;
uint8_t motor1_dir = 1;
uint8_t motor2_dir = 1;
uint8_t motor1_enable = 0;
uint8_t motor2_enable = 0;
uint8_t relay_state = 0;
bool ctrl_enable = false;

extern USB_Setup_TypeDef last_setup_pkt;
extern uint8_t *last_usb_data_ptr;
extern volatile bool config_write_pending;

void __attribute__ ((noinline)) enable_fpu(void) {
  // enable the FPU
  SCB->CPACR |= ((3UL << (10U * 2U)) | (3UL << (11U * 2U)));
}

// Serial debugging
// disabled due to pin conflict with PWM (use the JSON interface instead for debugging)

// USB debugging
// void debug_ring_callback(uart_ring *ring) {
//   char rcv;
//   while (getc(ring, &rcv) != 0) {
//     (void)putc(ring, rcv);
//   }
// }

// callback function to handle flash writes over USB
void usb_cb_ep0_out(void *usbdata_ep0, int len_ep0) {
  // Validate input parameters
  if (usbdata_ep0 == NULL || len_ep0 <= 0 || len_ep0 >= 512) {
    return;
  }
  
  // Validate data content for JSON RPC (must start with '{' for JSON)
  uint8_t *data = (uint8_t*)usbdata_ep0;
  if (len_ep0 > 0 && len_ep0 < 512 && data[0] == '{') {
    if (len_ep0 < 511) {
      ((char*)usbdata_ep0)[len_ep0] = '\0';
      json_rpc_handle_request((char*)usbdata_ep0, len_ep0);
    }
  }
  
  // Handle flash config writes with strict validation
  if ((usbdata_ep0 == last_usb_data_ptr) && (len_ep0 == sizeof(flash_config_t))) {
    if (config_write_pending) {
      handle_deferred_config_write();
    }
  }
}

int usb_cb_ep1_in(void *usbdata, int len, bool hardwired) {
  UNUSED(hardwired);
  CAN_FIFOMailBox_TypeDef *reply = (CAN_FIFOMailBox_TypeDef *)usbdata;
  int ilen = 0;
  while (ilen < MIN(len/0x10, 4) && can_pop(&can_rx_q, &reply[ilen])) {
    ilen++;
  }
  return ilen*0x10;
}
// send on serial, first byte to select the ring
void usb_cb_ep2_out(void *usbdata, int len, bool hardwired) {
  UNUSED(hardwired);
  UNUSED(len);
  UNUSED(usbdata);
}
// send on CAN
void usb_cb_ep3_out(void *usbdata, int len, bool hardwired) {
  UNUSED(usbdata);
  UNUSED(len);
  UNUSED(hardwired);
}
void usb_cb_ep3_out_complete() {
  if (can_tx_check_min_slots_free(MAX_CAN_MSGS_PER_BULK_TRANSFER)) {
    usb_outep3_resume_if_paused();
  }
}

void usb_cb_enumeration_complete() {
  // puts("USB enumeration complete\n");
  is_enumerated = 1;
}

int usb_cb_control_msg(USB_Setup_TypeDef *setup, uint8_t *resp, bool hardwired) {
  UNUSED(hardwired);
  unsigned int resp_len = 0;
  // uart_ring *ur = NULL;

  // Store setup for deferred processing
  memcpy(&last_setup_pkt, setup, sizeof(USB_Setup_TypeDef));
  last_usb_data_ptr = usbdata; 


  switch (setup->b.bRequest) {
    // **** 0xd1: enter bootloader mode
    case 0xd1:
      // this allows reflashing of the bootstub
      // so it's blocked over wifi
      switch (setup->b.wValue.w) {
        case 0:
          // only allow bootloader entry on debug builds
          #ifdef ALLOW_DEBUG
            if (hardwired) {
              // puts("-> entering bootloader\n");
              enter_bootloader_mode = ENTER_BOOTLOADER_MAGIC;
              NVIC_SystemReset();
            }
          #endif
          break;
        case 1:
          //puts("-> entering softloader\n");
          enter_bootloader_mode = ENTER_SOFTLOADER_MAGIC;
          NVIC_SystemReset();
          break;
        default:
          //puts("Bootloader mode invalid\n");
          break;
      }
      break;
    // **** 0xd8: reset ST
    case 0xd8:
      NVIC_SystemReset();
      break;
    case 0xf1:
      if (setup->b.wValue.w == 0xFFFFU) {
        //puts("Clearing CAN Rx queue\n");
        can_clear(&can_rx_q);
      } else if (setup->b.wValue.w < BUS_MAX) {
        //puts("Clearing CAN Tx queue\n");
        can_clear(can_queues[setup->b.wValue.w]);
      } else {
        //puts("Clearing CAN CAN ring buffer failed: wrong bus number\n");
      }
      break;
    case 0xFB: // JSON response output
      resp_len = json_rpc_get_response((char*)resp, setup->b.wValue.w, MAX_RESP_LEN);
      if (resp_len <= 0) {
        // puts("JSON RPC get response failed\n");
        resp_len = 0;
      }
      break;
    case 0xFC: // JSON command input
      // Data will be handled in usb_cb_ep0_out callback
      break;
    case 0xFD: {
      flash_unlock();
      flash_config_format();
      flash_lock();
      break;
    }
    case 0xFE: {  // Write config entry
      if (setup->b.wLength.w == sizeof(flash_config_t) &&
          setup->b.wValue.w < MAX_CONFIG_ENTRIES) {
        config_write_pending = true;
      }
      break;
    }
    case 0xFF: {  // Chunked config read
      uint16_t offset = setup->b.wValue.w;
      uint16_t length = setup->b.wLength.w;

      // Make sure we're not reading past the end of the config block
      const uint8_t *flash_bytes = (const uint8_t *)CONFIG_FLASH_ADDR;
      if (*(uint32_t *)flash_bytes == FLASH_CONFIG_MAGIC) {
        uint16_t max_len = MIN(length, MAX_RESP_LEN);  // cap to USB response size
        if (offset < sizeof(config_block_t)) {
          uint16_t remaining = sizeof(config_block_t) - offset;
          uint16_t copy_len = MIN(remaining, max_len);
          memcpy(resp, flash_bytes + offset, copy_len);
          resp_len = copy_len;
        } else {
          resp_len = 0;
        }
      } else {
        memset(resp, 0xFF, MIN(length, MAX_RESP_LEN));
        resp_len = MIN(length, MAX_RESP_LEN);
      }
      break;
    }
    default:
      break;
  }
  return resp_len;
}

// Mode management

void setup_mode(uint8_t mode) {
  current_mode = mode;

  switch (mode) {
    case MODE_STEER:
      mode_init_func = steer_init;
      mode_process_func = steer_process;
      mode_can_rx_handler_func = steer_can_rx_handler;
      mode_timer_handler_func = steer_timer_handler;
      break;
    case MODE_CRUISE:
      mode_init_func = cruise_init;
      mode_process_func = cruise_process;
      mode_can_rx_handler_func = cruise_can_rx_handler;
      mode_timer_handler_func = cruise_timer_handler;
      break;
    default:
      mode_init_func = default_init;
      mode_process_func = default_process;
      mode_can_rx_handler_func = default_can_rx_handler;
      mode_timer_handler_func = default_timer_handler;
      break;
  }
  
  if (mode_init_func) {
    mode_init_func();
  }
}

uint8_t detect_mode_from_flash(void) {
  const config_block_t *cfg = (const config_block_t *)CONFIG_FLASH_ADDR;
  
  if (!validate_flash_config(cfg)) {
    return MODE_DEFAULT;
  }
  
  const flash_config_t *sys_cfg = &cfg->entries[0];
  if (sys_cfg->cfg_type == CFG_TYPE_SYS) {
    uint8_t mode = sys_cfg->sys.cfg_extra[0];
    return mode;
  }
  
  return MODE_DEFAULT;
}

// CAN handlers

void CAN1_TX_IRQ_Handler(void) {
  // clear interrupt
  CAN1->TSR |= CAN_TSR_RQCP0;
}

void CAN1_RX0_IRQ_Handler(void) {
  while ((CAN1->RF0R & CAN_RF0R_FMP0) != 0) {
    int address = CAN1->sFIFOMailBox[0].RIR >> 21;
    uint8_t dat[8];
    for (int i = 0; i < 8; i++) {
      dat[i] = GET_BYTE(&CAN1->sFIFOMailBox[0], i);
    }
    if (mode_can_rx_handler_func) {
      mode_can_rx_handler_func(address, dat);
    }
    CAN1->RF0R |= CAN_RF0R_RFOM0;
  }
}

void CAN1_SCE_IRQ_Handler(void) {
  state = FAULT_SCE;
  llcan_clear_send(CAN1);
}


void TIM3_IRQ_Handler(void) {
  if (mode_timer_handler_func) {
    mode_timer_handler_func();
  }
  
  if (usb_ctrl_active) {
    ctrl_timeout++;
    if (ctrl_timeout > USB_CTRL_TIMEOUT) {
      usb_ctrl_active = false;
      ctrl_timeout = 0;
    }
  }
  
  TIM3->SR = 0;
}

void TIM1_BRK_TIM9_IRQ_Handler(void) {
  if (usb_ctrl_active) {
    ctrl_timeout++;
    if (ctrl_timeout > USB_CTRL_TIMEOUT) {
      usb_ctrl_active = false;
      ctrl_timeout = 0;
    }
  }
  TIM9->SR = 0;
}

void EXTI9_5_IRQ_Handler(void) {
  volatile unsigned int pr = EXTI->PR & (1U << 9);
  if ((pr & (1U << 9)) != 0U) {
    EXTI->PR = (1U << 9);
  }
}

// Main
void loop(void) {
  if (mode_process_func) {
    mode_process_func();
  }
}

int main(void) {
  // ############## FLASH HANDLING #####################
  config_block_t current_cfg_in_ram;
  memcpy(&current_cfg_in_ram, (void *)CONFIG_FLASH_ADDR, sizeof(config_block_t));

  if (!validate_flash_config(&current_cfg_in_ram)) {
    // flash_unlock();
    // flash_config_format();
    // flash_lock();
    // NVIC_SystemReset();
  } else {
    init_config_pointers(&current_cfg_in_ram);
  }

  // ###################################################################

  // Init interrupt table
  init_interrupts(true);

  REGISTER_INTERRUPT(CAN1_TX_IRQn, CAN1_TX_IRQ_Handler, CAN_INTERRUPT_RATE, FAULT_INTERRUPT_RATE_CAN_1)
  REGISTER_INTERRUPT(CAN1_RX0_IRQn, CAN1_RX0_IRQ_Handler, CAN_INTERRUPT_RATE, FAULT_INTERRUPT_RATE_CAN_1)
  REGISTER_INTERRUPT(CAN1_SCE_IRQn, CAN1_SCE_IRQ_Handler, CAN_INTERRUPT_RATE, FAULT_INTERRUPT_RATE_CAN_1)

  // Should run at around 732Hz (see init below)
  REGISTER_INTERRUPT(TIM3_IRQn, TIM3_IRQ_Handler, 1000U, FAULT_INTERRUPT_RATE_TIM3)

  // // 8Hz timer
  REGISTER_INTERRUPT(TIM1_BRK_TIM9_IRQn, TIM1_BRK_TIM9_IRQ_Handler, 10U, FAULT_INTERRUPT_RATE_TIM9)

  disable_interrupts();

  // init devices
  clock_init();
  peripherals_init();
  enable_fpu();
  
  // No debug UART - PWM uses PA2/PA3
  detect_configuration();
  detect_board_type();

  // init board
  current_board->init();
  USBx->GOTGCTL |= USB_OTG_GOTGCTL_BVALOVAL;
  USBx->GOTGCTL |= USB_OTG_GOTGCTL_BVALOEN;
  usb_init();

  // 8hz
  // TODO: use this timer for something
  // timer_init(TIM9, 183);
  // NVIC_EnableIRQ(TIM1_BRK_TIM9_IRQn);
  // REGISTER_INTERRUPT(EXTI9_5_IRQn, EXTI9_5_IRQ_Handler, 0xFFFF, FAULT_INTERRUPT_RATE_TACH)
  // register_set(&(SYSCFG->EXTICR[3]), SYSCFG_EXTICR3_EXTI9_PA, 0x00U);
  // register_set_bits(&(EXTI->IMR), (1U << 9));
  // register_set_bits(&(EXTI->RTSR), (1U << 9));
  // register_set_bits(&(EXTI->FTSR), (1U << 9));
  // NVIC_EnableIRQ(EXTI9_5_IRQn);

  // ADC
  adc_init();

  // init can
  bool llcan_speed_set = llcan_set_speed(CAN1, 5000, false, false);
  if (!llcan_speed_set) {
    //puts("Failed to set llcan speed");
  }

  bool ret = llcan_init(CAN1);
  UNUSED(ret);

  // 48mhz / 65536 ~= 732
  timer_init(TIM3, 15);
  NVIC_EnableIRQ(TIM3_IRQn);

  // ============ GPIO SETUP ============
    
  // ADC input
  set_gpio_mode(GPIOC, 3, MODE_ANALOG);
  
  // Motor 1
  set_gpio_mode(GPIOA, 2, MODE_OUTPUT);
  set_gpio_mode(GPIOB, 10, MODE_OUTPUT);
  set_gpio_mode(GPIOB, 0, MODE_OUTPUT);
  // set_gpio_output_type(GPIOA, 2, OUTPUT_TYPE_PUSH_PULL);
  set_gpio_output_type(GPIOB, 10, OUTPUT_TYPE_PUSH_PULL);
  set_gpio_output_type(GPIOB, 0, OUTPUT_TYPE_PUSH_PULL);
  // set_gpio_pullup(GPIOA, 2, PULL_DOWN);
  set_gpio_pullup(GPIOB, 10, PULL_UP);
  set_gpio_pullup(GPIOB, 0, PULL_DOWN);
  // set_gpio_output(GPIOA, 2, 0);
  set_gpio_output(GPIOB, 10, 0); 
  set_gpio_output(GPIOB, 0, 1);
  
  // Motor 2
  set_gpio_mode(GPIOA, 3, MODE_OUTPUT);
  set_gpio_mode(GPIOB, 3, MODE_OUTPUT);
  set_gpio_mode(GPIOB, 1, MODE_OUTPUT);
  // set_gpio_output_type(GPIOA, 3, OUTPUT_TYPE_PUSH_PULL);
  set_gpio_output_type(GPIOB, 3, OUTPUT_TYPE_PUSH_PULL);
  set_gpio_output_type(GPIOB, 1, OUTPUT_TYPE_PUSH_PULL);
  // set_gpio_pullup(GPIOA, 3, PULL_DOWN);
  set_gpio_pullup(GPIOB, 3, PULL_UP);
  set_gpio_pullup(GPIOB, 1, PULL_DOWN);
  // set_gpio_output(GPIOA, 3, 0);
  set_gpio_output(GPIOB, 3, 0);  
  set_gpio_output(GPIOB, 1, 1);
  
  // RELAY (PB4)
  set_gpio_mode(GPIOB, 4, MODE_OUTPUT);
  set_gpio_output_type(GPIOB, 4, OUTPUT_TYPE_PUSH_PULL);
  set_gpio_pullup(GPIOB, 4, PULL_DOWN);
  set_gpio_output(GPIOB, 4, 1); 

  // enable the FPU
  enable_fpu();
  // setup microsecond timer
  // realoads every 4ish seconds
  TIM2->PSC = 479; //48-1;
  TIM2->ARR = 99999; 
  TIM2->DIER |= TIM_DIER_UIE;
  TIM2->CR1 = TIM_CR1_CEN;
  TIM2->EGR = TIM_EGR_UG;
  // use TIM2->CNT to read
  // reset with TIM2->CNT = 0;

  // NVIC_EnableIRQ(TIM2_IRQn);

  gen_crc_lookup_table(crc_poly, crc8_lut_1d);

  if (signal_configs[0] != NULL && (signal_configs[0]->sys.iwdg_en & 1)){
    watchdog_init();
  }

  json_rpc_init(actuator_methods); 

  // Setup mode system
  uint8_t mode = detect_mode_from_flash();
  setup_mode(mode);
  
  // pwm on PA2, PA3
  set_gpio_mode(GPIOA, 2, MODE_ALTERNATE);
  set_gpio_mode(GPIOA, 3, MODE_ALTERNATE);
  set_gpio_alternate(GPIOA, 2, GPIO_AF3_TIM9);
  set_gpio_alternate(GPIOA, 3, GPIO_AF3_TIM9);
  RCC->APB2ENR |= RCC_APB2ENR_TIM9EN;
  pwm_init(TIM9, 1);
  pwm_init(TIM9, 2);

  //puts("**** INTERRUPTS ON ****\n");
  enable_interrupts();
  adc[0] = 0;
  adc[1] = 0;
  // main program loop
  while (1) {
    loop();
  }

  return 0;
}

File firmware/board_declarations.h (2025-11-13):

// ******************** Prototypes ********************
typedef void (*board_init)(void);
typedef void (*board_enable_can_transceiver)(uint8_t transceiver, bool enabled);
typedef void (*board_enable_can_transceivers)(bool enabled);
typedef void (*board_set_led)(uint8_t color, bool enabled);
typedef void (*board_set_usb_power_mode)(uint8_t mode);
typedef void (*board_set_gps_mode)(uint8_t mode);
typedef void (*board_set_can_mode)(uint8_t mode);
typedef void (*board_usb_power_mode_tick)(uint32_t uptime);
typedef bool (*board_check_ignition)(void);
typedef uint32_t (*board_read_current)(void);
typedef void (*board_set_ir_power)(uint8_t percentage);
typedef void (*board_set_fan_power)(uint8_t percentage);
typedef void (*board_set_phone_power)(bool enabled);
typedef void (*board_set_clock_source_mode)(uint8_t mode);
typedef void (*board_set_siren)(bool enabled);

struct board {
  const char *board_type;
  const harness_configuration *harness_config;
  board_init init;
  board_enable_can_transceiver enable_can_transceiver;
  board_enable_can_transceivers enable_can_transceivers;
  board_set_led set_led;
  board_set_usb_power_mode set_usb_power_mode;
  board_set_gps_mode set_gps_mode;
  board_set_can_mode set_can_mode;
  board_usb_power_mode_tick usb_power_mode_tick;
  board_check_ignition check_ignition;
  board_read_current read_current;
  board_set_ir_power set_ir_power;
  board_set_fan_power set_fan_power;
  board_set_phone_power set_phone_power;
  board_set_clock_source_mode set_clock_source_mode;
  board_set_siren set_siren;
};

// ******************* Definitions ********************
// These should match the enums in cereal/log.capnp and __init__.py
#define HW_TYPE_UNKNOWN 0U
#define HW_TYPE_WHITE_PANDA 1U
#define HW_TYPE_GREY_PANDA 2U
#define HW_TYPE_BLACK_PANDA 3U

#define HW_TYPE_UNO 5U
#define HW_TYPE_DOS 6U
#define HW_TYPE_GATEWAY 8U

// LED colors
#define LED_RED 0U
#define LED_GREEN 1U
#define LED_BLUE 2U

// USB power modes (from cereal.log.health)
#define USB_POWER_NONE 0U
#define USB_POWER_CLIENT 1U
#define USB_POWER_CDP 2U
#define USB_POWER_DCP 3U

// GPS modes
#define GPS_DISABLED 0U
#define GPS_ENABLED 1U
#define GPS_BOOTMODE 2U

// CAN modes
#define CAN_MODE_NORMAL 0U
#define CAN_MODE_GMLAN_CAN2 1U
#define CAN_MODE_GMLAN_CAN3 2U
#define CAN_MODE_OBD_CAN2 3U

// ********************* Globals **********************
uint8_t usb_power_mode = USB_POWER_NONE;

// ************ Board function prototypes *************
bool board_has_gps(void);
bool board_has_gmlan(void);
bool board_has_obd(void);
bool board_has_lin(void);
bool board_has_rtc(void);
bool board_has_relay(void);

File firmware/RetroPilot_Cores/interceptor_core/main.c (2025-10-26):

// ********************* Includes *********************
#include "../../config.h"
#include "libc.h"

#include "main_declarations.h"
#include "critical.h"
#include "faults.h"

#include "drivers/registers.h"
#include "drivers/interrupts.h"
#include "drivers/llcan.h"
#include "drivers/llgpio.h"
#include "drivers/adc.h"

#include "board.h"

#include "drivers/clock.h"
#include "drivers/dac.h"
#include "drivers/timer.h"

#include "gpio.h"
#include "crc.h"

#define CAN CAN1

#define DEBUG

#define USB_STRING_DESCRIPTORS

#define STRING_DESCRIPTOR_HEADER(size) \
  (((((size) * 2) + 2) & 0xFF) | 0x0300)

static const uint16_t string_manufacturer_desc[] = {
  STRING_DESCRIPTOR_HEADER(10),
  'R','e','t','r','o','P','i','l','o','t'
};

static const uint16_t string_product_desc[] = {
  STRING_DESCRIPTOR_HEADER(16),
  'I','n','t','e','r','c','e','p','t','o','r',' ','C','o','r','e'
};

#include "drivers/uart.h"
#include "chimera/usb.h"
#include "chimera/chimera.h"
#include "drivers/json_rpc.h"
#include "RetroPilot_Cores/interceptor_core/torque_lut.h"
#include "RetroPilot_Cores/interceptor_core/modes/common.h"
#include "RetroPilot_Cores/interceptor_core/json_rpc_handlers.h"

extern uint8_t usbdata[0x100];
extern uart_ring uart_ring_debug;

#define MODE_UNCONFIGURED 0
#define MODE_DIFFERENTIAL 1
#define MODE_GAS_PEDAL    2

#include "RetroPilot_Cores/interceptor_core/modes/default.h"
#include "RetroPilot_Cores/interceptor_core/modes/differential.h"
#include "RetroPilot_Cores/interceptor_core/modes/gas_pedal.h"

void (*mode_init_func)(void);
void (*mode_process_func)(void);
void (*mode_can_rx_handler_func)(int address, uint8_t *dat);
void (*mode_timer_handler_func)(void);
bool (*mode_validate_adc_func)(uint32_t adc_val, uint8_t channel);
void (*mode_debug_output_func)(bool relay_state);
uint8_t current_mode = MODE_UNCONFIGURED;

uint32_t enter_bootloader_mode;

#define USB_CTRL_TIMEOUT 4
uint32_t ctrl_timeout = 0;
volatile bool usb_ctrl_active = false;

#define ENTER_BOOTLOADER_MAGIC 0xdeadbeef
#define ENTER_SOFTLOADER_MAGIC 0xdeadc0de

void usb_cb_ep0_out(void *usbdata_ep0, int len_ep0) {
  // Validate input parameters
  if (usbdata_ep0 == NULL || len_ep0 <= 0 || len_ep0 >= 512) {
    return;
  }
  
  // Validate data content for JSON RPC (must start with '{' for JSON)
  uint8_t *data = (uint8_t*)usbdata_ep0;
  if (len_ep0 > 0 && len_ep0 < 512 && data[0] == '{') {
    if (len_ep0 < 511) {
      ((char*)usbdata_ep0)[len_ep0] = '\0';
      if (!json_rpc_handle_request((char*)usbdata_ep0, len_ep0)) {
        puts("JSON RPC handle request failed\n");
      }
    }
  }
  
  // Handle flash config writes with strict validation
  if ((usbdata_ep0 == last_usb_data_ptr) && (len_ep0 == sizeof(flash_config_t))) {
    if (config_write_pending) {
      handle_deferred_config_write();
    }
  }
}

// External declarations for chimera.h static variables
extern USB_Setup_TypeDef last_setup_pkt;
extern uint8_t *last_usb_data_ptr;
extern volatile bool config_write_pending;

// cppcheck-suppress unusedFunction ; used in headers not included in cppcheck
void __initialize_hardware_early(void) {
  early();
}

void debug_ring_callback(uart_ring *ring) {
  char rcv;
  while (getc(ring, &rcv) != 0) {
    (void)putc(ring, rcv);
  }
}

int usb_cb_ep1_in(void *usbdata, int len, bool hardwired) {
  UNUSED(usbdata);
  UNUSED(len);
  UNUSED(hardwired);
  return 0;
}
void usb_cb_ep2_out(void *usbdata, int len, bool hardwired) {
  UNUSED(usbdata);
  UNUSED(len);
  UNUSED(hardwired);
}
void usb_cb_ep3_out(void *usbdata, int len, bool hardwired) {
  UNUSED(usbdata);
  UNUSED(len);
  UNUSED(hardwired);
}
void usb_cb_ep3_out_complete(void) {}
void usb_cb_enumeration_complete(void) {}

int usb_cb_control_msg(USB_Setup_TypeDef *setup, uint8_t *resp, bool hardwired) {
  UNUSED(hardwired);
  unsigned int resp_len = 0;
  uart_ring *ur = NULL;

  // Store setup for deferred processing
  memcpy(&last_setup_pkt, setup, sizeof(USB_Setup_TypeDef));
  last_usb_data_ptr = usbdata;

  switch (setup->b.bRequest) {
    // **** 0xd1: enter bootloader mode
    case 0xd1:
      switch (setup->b.wValue.w) {
        case 0:
          // only allow bootloader entry on debug builds
          #ifdef ALLOW_DEBUG
            if (hardwired) {
              puts("-> entering bootloader\n");
              enter_bootloader_mode = ENTER_BOOTLOADER_MAGIC;
              NVIC_SystemReset();
            }
          #endif
          break;
        case 1:
          puts("-> entering softloader\n");
          enter_bootloader_mode = ENTER_SOFTLOADER_MAGIC;
          NVIC_SystemReset();
          break;
        default:
          puts("Bootloader mode invalid\n");
          break;
      }
      break;
    // **** 0xd8: reset ST
    case 0xd8:
      NVIC_SystemReset();
      break;
    // **** 0xdd: get interceptor mode
    case 0xdd:
      resp[0] = current_mode;
      resp_len = 1;
      break;
    // **** 0xe0: uart read
    case 0xe0:
      ur = get_ring_by_number(setup->b.wValue.w);      
      // read
      if (!ur) {
        break;
      }
      while ((resp_len < MIN(setup->b.wLength.w, MAX_RESP_LEN)) &&
                         getc(ur, (char*)&resp[resp_len])) {
        ++resp_len;
      }
      break;
    case 0xFB: // JSON response output
      resp_len = json_rpc_get_response((char*)resp, setup->b.wValue.w, MAX_RESP_LEN);
      if (resp_len <= 0) {
        puts("JSON RPC get response failed\n");
        resp_len = 0;
      }
      break;
    case 0xFC: // JSON command input
      // Data will be handled in usb_cb_ep0_out callback
      break;
    // **** 0xFD: flash config format
    case 0xFD: {
      flash_unlock();
      flash_config_format();
      flash_lock();
      break;
    }
    case 0xFF: {  // Chunked config read
      uint16_t offset = setup->b.wValue.w;
      uint16_t length = setup->b.wLength.w;
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

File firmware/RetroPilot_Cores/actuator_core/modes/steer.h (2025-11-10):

#pragma once
#include "common.h"

// Steer-specific variables
static int16_t steer_torque_req;
static int16_t steer_angle_req;
static uint8_t steer_mode;

// placeholder logic just to test this mode of Actuator Core
// TODO: actually write something useable

static void steer_init(void) {
  steer_torque_req = 0;
  steer_angle_req = 0;
  steer_mode = 0;
}

static void steer_process(void) {
  adc[0] = adc_get(12);
  adc[1] = adc_get(13);
  
  // Convert torque request to motor speeds
  // Positive torque = turn right, negative = turn left
  int16_t motor1_speed = 0;  // Left motor
  int16_t motor2_speed = 0;  // Right motor
  
  if (enabled && (steer_torque_req != 0 || steer_angle_req != 0)) {
    if (steer_mode == 0) {  // Torque mode
      // Simple differential: one motor forward, one reverse
      if (steer_torque_req > 0) {  // Turn right
        motor1_speed = steer_torque_req / 10;   // Scale down
        motor2_speed = -steer_torque_req / 10;
      } else {  // Turn left
        motor1_speed = steer_torque_req / 10;
        motor2_speed = -steer_torque_req / 10;
      }
    } else {  // Angle mode (future implementation)
      motor1_speed = 0;
      motor2_speed = 0;
    }
    
    // Limit speeds to 0-100%
    if (motor1_speed > 100) motor1_speed = 100;
    if (motor1_speed < -100) motor1_speed = -100;
    if (motor2_speed > 100) motor2_speed = 100;
    if (motor2_speed < -100) motor2_speed = -100;
    
    // Set motor directions and PWM
    set_gpio_output(GPIOB, 10, 0);  // Enable motor1
    set_gpio_output(GPIOB, 3, 0);   // Enable motor2
    set_gpio_output(GPIOB, 0, motor1_speed >= 0 ? 1 : 0);  // Motor1 direction
    set_gpio_output(GPIOB, 1, motor2_speed >= 0 ? 1 : 0);  // Motor2 direction
    
    pwm_set(TIM9, 1, motor1_speed >= 0 ? motor1_speed : -motor1_speed);
    pwm_set(TIM9, 2, motor2_speed >= 0 ? motor2_speed : -motor2_speed);
  } else {
    // Disable motors
    set_gpio_output(GPIOB, 10, 1);  // Disable motor1
    set_gpio_output(GPIOB, 3, 1);   // Disable motor2
    pwm_set(TIM9, 1, 0);
    pwm_set(TIM9, 2, 0);
  }
  
  watchdog_feed();
}

static void steer_can_rx_handler(int address, uint8_t *dat) {
  if (address == CAN_STEER_INPUT) {
    // Bootloader entry
    if (GET_BYTES_04(&CAN1->sFIFOMailBox[0]) == 0xdeadface) {
      if (GET_BYTES_48(&CAN1->sFIFOMailBox[0]) == 0x0ab00b1e) {
        enter_bootloader_mode = ENTER_SOFTLOADER_MAGIC;
        NVIC_SystemReset();
      } else if (GET_BYTES_48(&CAN1->sFIFOMailBox[0]) == 0x02b00b1e) {
        enter_bootloader_mode = ENTER_BOOTLOADER_MAGIC;
        NVIC_SystemReset();
      }
    }
    
    // Parse ACTUATOR_STEERING_COMMAND
    steer_torque_req = (int16_t)((dat[5] << 8) | dat[4]);  // REQUESTED_STEER_TORQUE
    steer_angle_req = (int16_t)((dat[3] << 8) | dat[2]);   // REQUESTED_STEER_ANGLE
    steer_mode = (dat[1] >> 4) & 0x3;                      // STEER_MODE
    uint8_t counter = dat[1] & 0xF;                        // COUNTER
    uint8_t checksum = dat[0];                             // CHECKSUM
    
    if (checksum == lut_checksum(dat, 6, crc8_lut_1d)) {
      if (((current_index + 1U) & COUNTER_CYCLE) == counter) {
        enabled = (steer_torque_req != 0 || steer_angle_req != 0) ? 1 : 0;
        timeout = 0;
        state = NO_FAULT;
      }
      current_index = counter;
    } else {
      state = FAULT_BAD_CHECKSUM;
    }
  }
}

static void steer_timer_handler(void) {
  if ((CAN1->TSR & CAN_TSR_TME0) == CAN_TSR_TME0) {
    uint8_t dat[7];
    // ACTUATOR_STEERING_STATUS format
    dat[1] = (adc[0] >> 0) & 0xFFU;        // STEERING_TORQUE_DRIVER low
    dat[2] = (adc[0] >> 8) & 0xFFU;        // STEERING_TORQUE_DRIVER high
    dat[3] = (adc[1] >> 0) & 0xFFU;        // STEERING_TORQUE_EPS low
    dat[4] = (adc[1] >> 8) & 0xFFU;        // STEERING_TORQUE_EPS high
    dat[5] = (enabled ? 1 : 0) | ((state & 0xF) << 4);  // STEERING_OK | STATUS
    dat[6] = pkt_idx & 0xF;                // COUNTER
    dat[0] = lut_checksum(dat, 7, crc8_lut_1d);  // CHECKSUM
    
    CAN_FIFOMailBox_TypeDef to_send;
    to_send.RDLR = dat[0] | (dat[1] << 8) | (dat[2] << 16) | (dat[3] << 24);
    to_send.RDHR = dat[4] | (dat[5] << 8) | (dat[6] << 16);
    to_send.RDTR = 7;
    to_send.RIR = (CAN_STEER_OUTPUT << 21) | 1U;
    can_send(&to_send, 0, false);
    llcan_clear_send(CAN1);
    ++pkt_idx;
    pkt_idx &= COUNTER_CYCLE;
  } else {
    state = FAULT_SEND;
  }
}

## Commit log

2022-12-28 bom and pnp CSV files
    [bom.csv, pnp.csv]
2022-12-28 bom xlsx
    [bom.xlsx]
2023-06-29 move ocelot-gw, upload ocelot-pro, make readme
    [bom.csv, bom.xlsx, ocelot-gw.brd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]
2023-07-19 CAN motor control example
2023-08-21 follow distance button
2023-09-18 steer actuator demo
2023-09-25 Actuator demo readme
2023-09-25 add STL files
    [casing_front.stl, casing_rear.stl, driven_gear.stl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]
2024-01-28 Fix taking data from wrong CAN bus
    [main.c]
2024-01-28 minor fix for generating Toyota checksum after can message construction
    [main.c]
2024-01-28 Change set value to all hex
    On my test the old one doesn't work and I don't know why. these works in my testing.
    [main.c]
2025-02-04 Update README.MD
    add David Abraham to actuator mechanical design credits
2025-02-12 fixes for steering interceptor
    [main.c]
2025-02-23 throttle controller, BCM initial upload
2025-03-27 relay_core cleanup pre-testing
2025-03-28 setup GPIOs for Actuator Core
2025-06-09 REV3 PCB testing with joystick
2025-06-27 add steer rate config field, move stuff out of main.c
2025-07-15 fix a bug in ibst that prevented OP from engaging nicely
    [main.c, stm_flash_config.py]
2025-07-26 torque maps for Interceptor Core, vss calculation for Chimera
2025-09-22 ibst fixes, relay_core feature added: remap GPIO
    [chimera.h, main.c, stm_flash_config.py]
2025-09-23 WIP: relay core interactive config
2025-10-01 WIP relay core: work on interrupts, output json chimera: engine RPM and crank angle
2025-10-03 resolve #20 JSON I/O over USB
    [chimera.h, main.c]
2025-10-17 fixes to JSON RPC and interceptor core JSON implementation
    [common.h, default.h, differential.h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]
2025-10-24 JSON RPC improvements, Actuator Core mode setting
2025-11-10 Actuator Core: mode configs and new settings for motor bridge channels
2025-11-13 throttle command scaling
2025-11-13 remove references to pedal to fix compilation
    [board_declarations.h]

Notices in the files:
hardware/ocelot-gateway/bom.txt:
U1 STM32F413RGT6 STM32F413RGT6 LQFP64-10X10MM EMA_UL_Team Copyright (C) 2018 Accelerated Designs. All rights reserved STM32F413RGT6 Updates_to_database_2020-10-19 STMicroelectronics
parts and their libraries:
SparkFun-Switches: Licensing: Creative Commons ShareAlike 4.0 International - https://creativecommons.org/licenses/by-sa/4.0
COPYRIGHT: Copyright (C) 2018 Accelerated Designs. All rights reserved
